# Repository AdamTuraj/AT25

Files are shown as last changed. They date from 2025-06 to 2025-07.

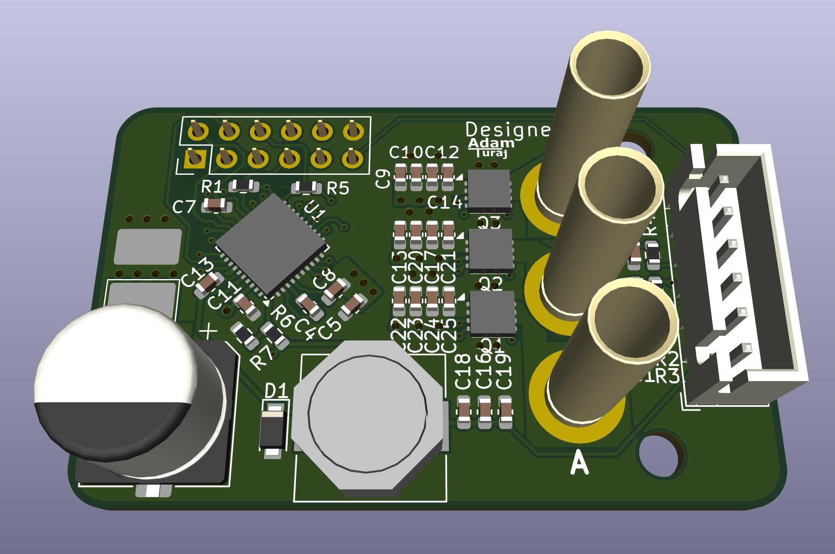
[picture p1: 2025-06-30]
Hardware/Motor_Driver/Images/3D View.png

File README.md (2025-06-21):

# AT25 - A cooler RC Car

The goal of this project is to build experience for a potential future in motorsports / Formula Student. As a fan of road car racing, I will be designing the aero and suspension car roughly around the LMGT3 regulations.

### Requirements

Below are the goals of this project. The self-imposed regulations I will be following when designing the car:

- Aerodynamic elements that work and are CFD optimized
- Double Wishbone suspension
- AWD with one sensored brushless motors
- Braking with the electric motor
- Mostly made of plastic with the exception of:
  - Gearing in the diffs
  - The electronic parts
  - The wheels
  - Any gaskets that may be required
  - Fasteners
- Remote controlled
- Fits a Lego mini figure in a driver seat

### Journal

I will be recording my day to day work in a journal found [here](https://github.com/AdamTuraj/AT25/blob/main/JOURNAL.md)

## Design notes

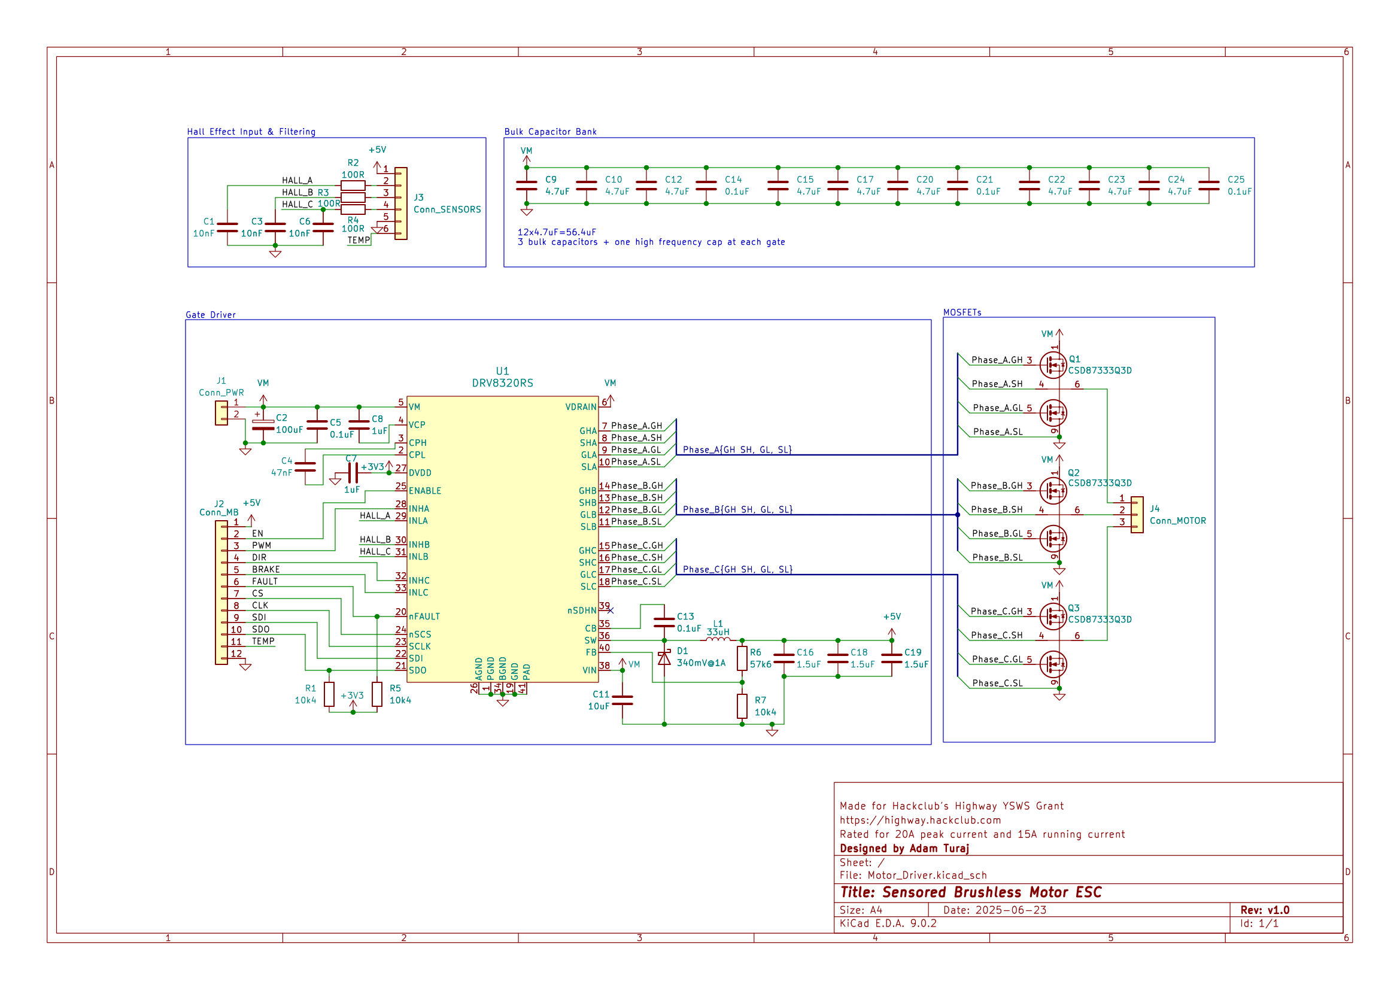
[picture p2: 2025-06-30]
Hardware/Motor_Driver/Images/Schematic.png

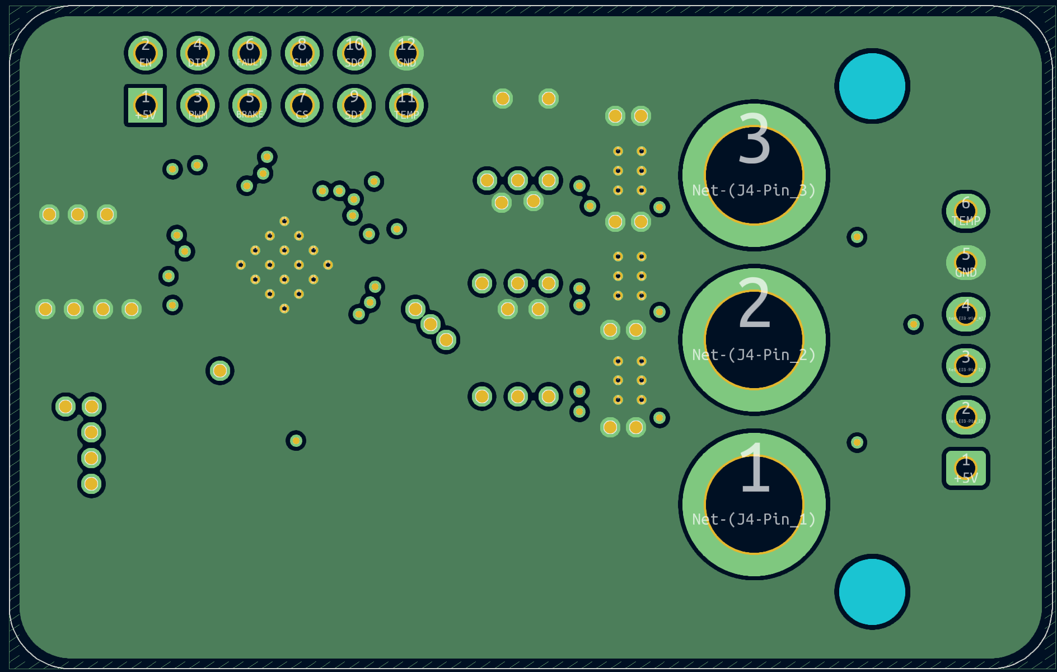
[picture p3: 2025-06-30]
Hardware/Motor_Driver/Images/2nd (GND).png

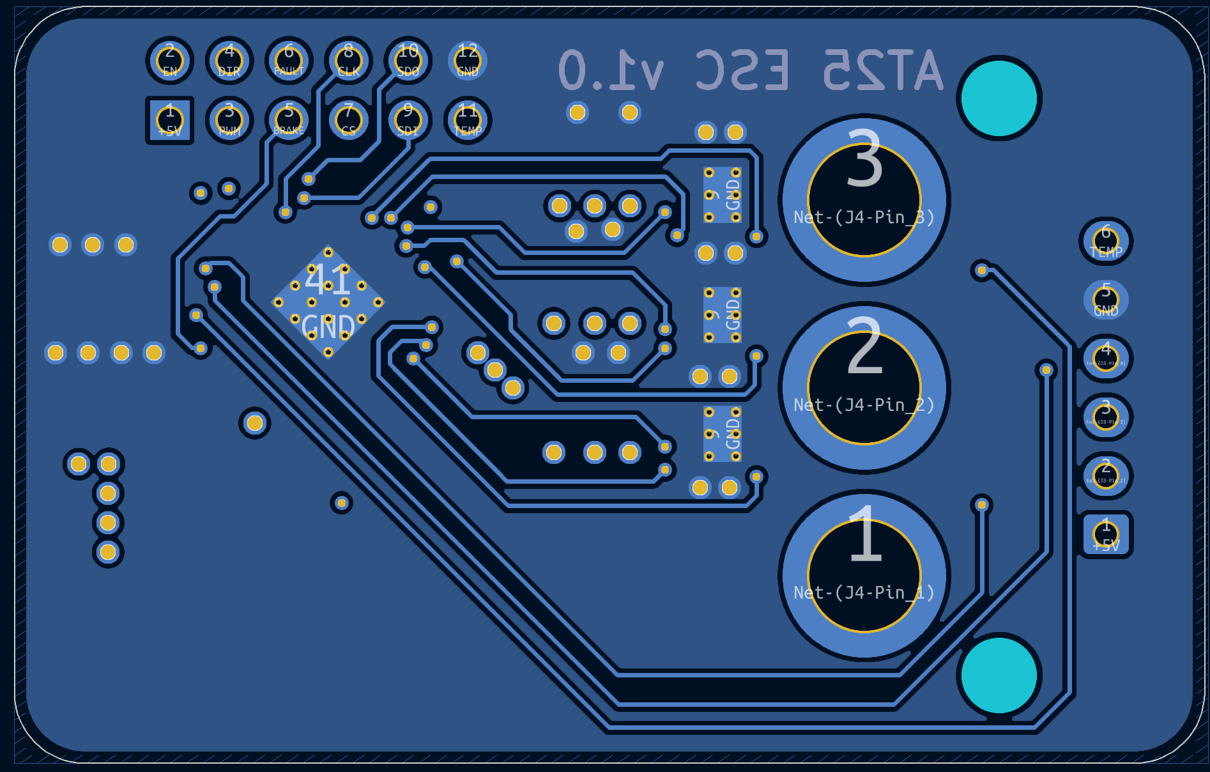
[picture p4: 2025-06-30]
Hardware/Motor_Driver/Images/Bottom (Sig).png

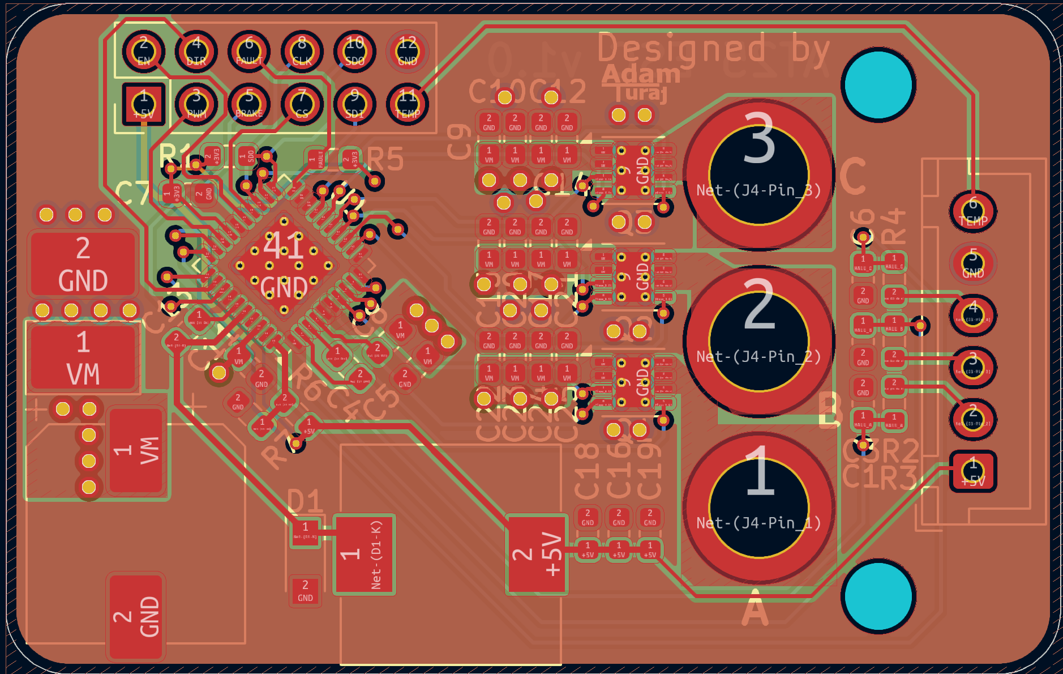
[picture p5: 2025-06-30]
Hardware/Motor_Driver/Images/All Layers.png

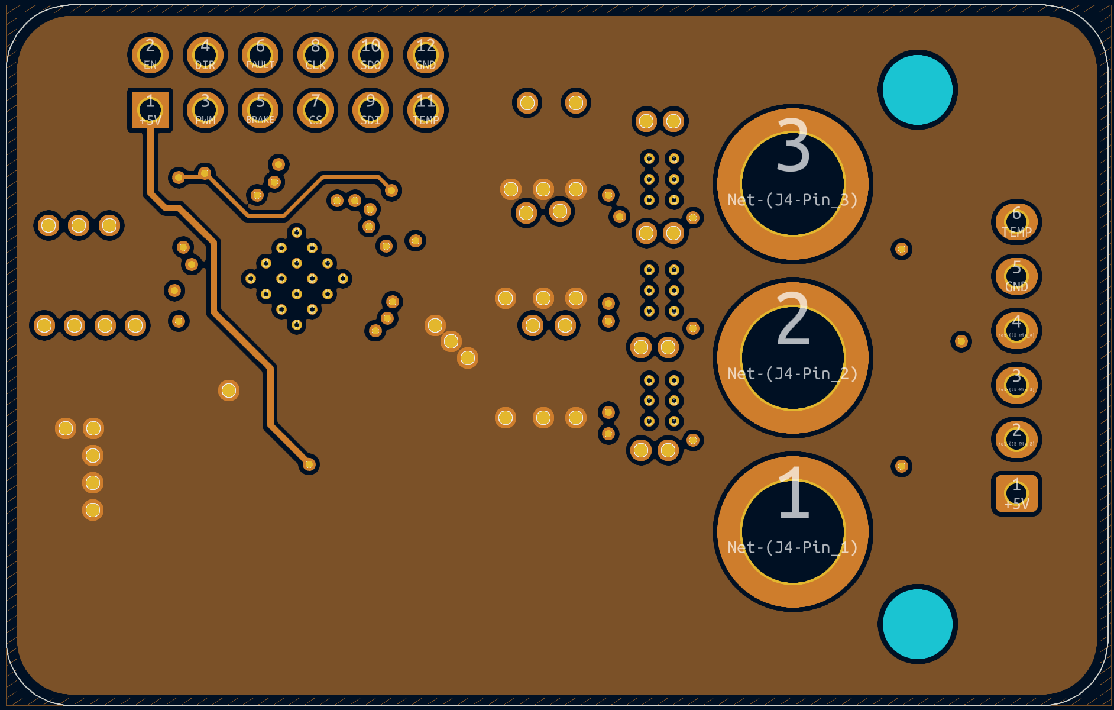
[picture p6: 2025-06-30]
Hardware/Motor_Driver/Images/3rd (PWR).png

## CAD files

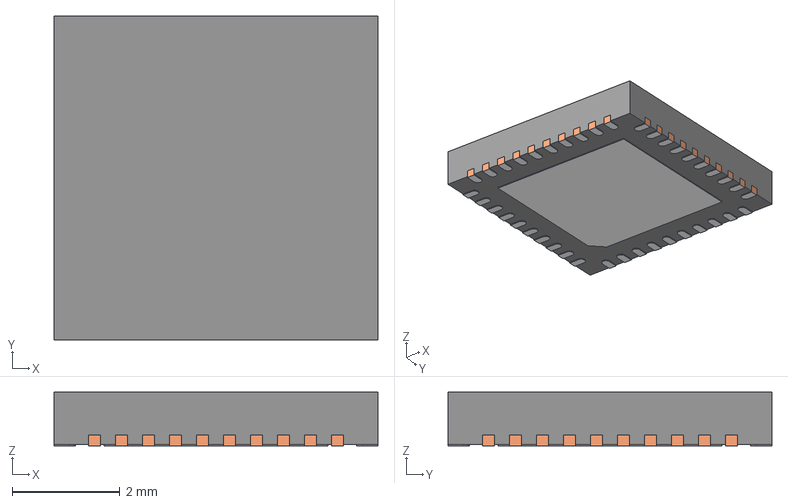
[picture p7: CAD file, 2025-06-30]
Hardware/Motor_Driver/STEP/RHA0040B.stp
6.00 x 6.00 x 1.00 mm
BODY-QFN
FRAME-RHA0040B
PIN1-ID

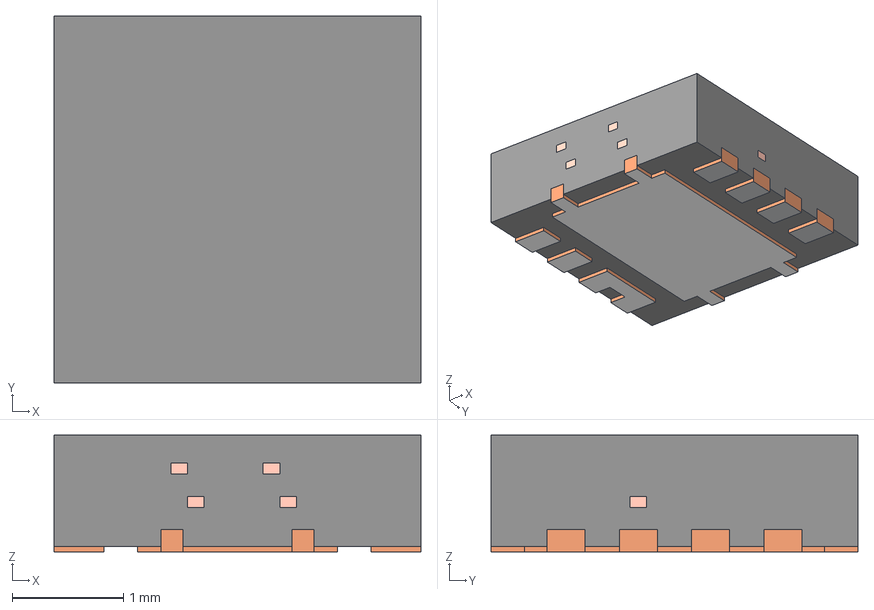
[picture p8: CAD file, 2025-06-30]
Hardware/Motor_Driver/STEP/DPB0008A.stp
3.30 x 3.30 x 1.05 mm
BODY-SON
FRAME-DPB0008A
DPB0008A_CLIP

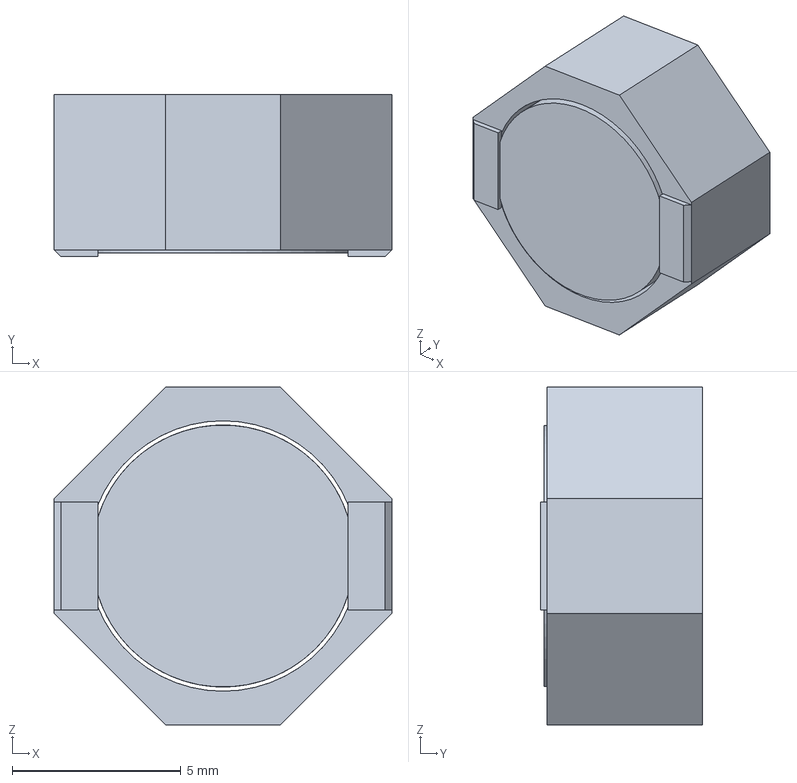
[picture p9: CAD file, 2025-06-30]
Hardware/Motor_Driver/STEP/sru1048.stp
10.0 x 4.80 x 10.0 mm

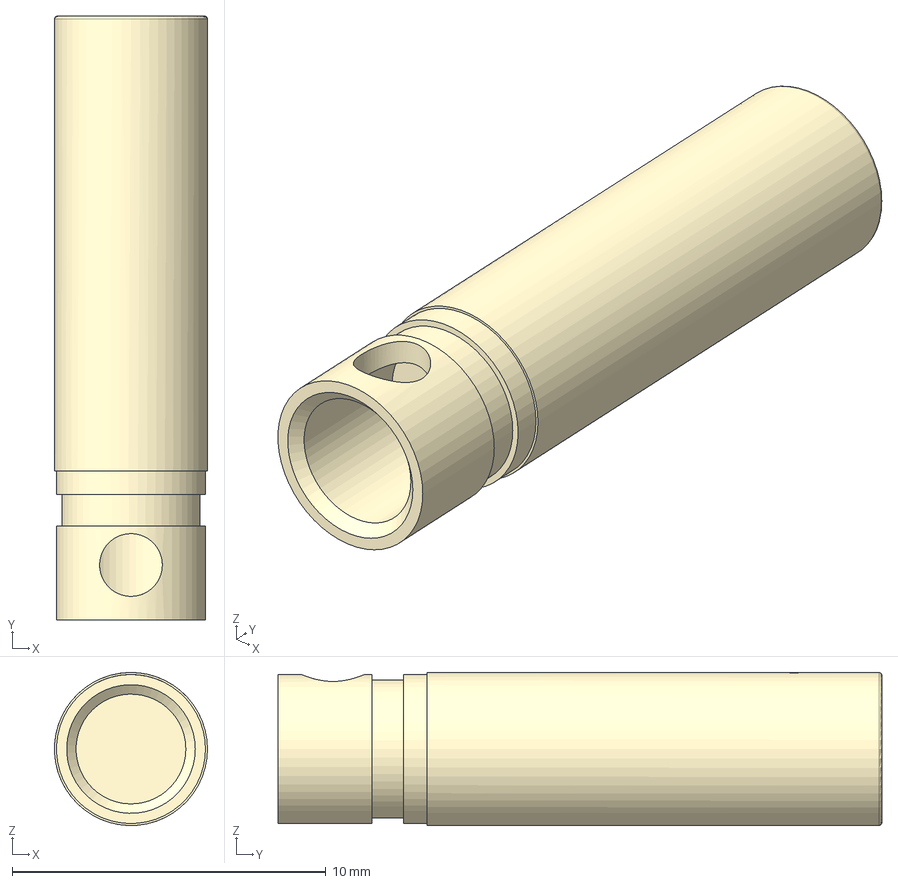
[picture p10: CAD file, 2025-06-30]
Hardware/Motor_Driver/STEP/Female_4mm_Bullet_Connector.step
4.88 x 19.2 x 4.88 mm

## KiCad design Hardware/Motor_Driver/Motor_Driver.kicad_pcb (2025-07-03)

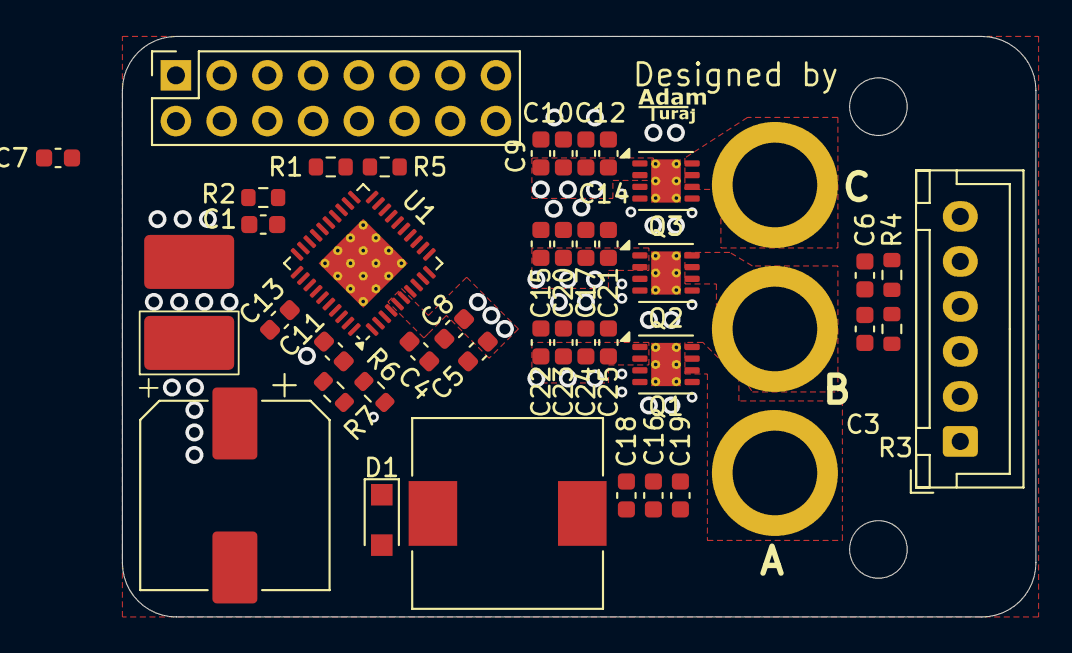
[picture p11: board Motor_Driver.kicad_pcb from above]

Board: 4 copper layers, 50.8 x 32.2 mm, 42 parts (0 on the bottom side), 38 nets, no tracks yet.

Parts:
C1, C3, C6: 10nF; C_0603_1608Metric
C2: 100uF; CP_Elec_10x10
C4: 47nF; C_0603_1608Metric
C5, C13, C14, C21, C25: 0.1uF; C_0603_1608Metric
C7, C8: 1uF; C_0603_1608Metric
C9, C10, C12, C15, C17, C20, C22, C23, C24: 4.7uF; C_0603_1608Metric
C11: 10uF; C_0603_1608Metric
C16, C18, C19: 1.5uF; C_0603_1608Metric
D1: 340mV@1A; Nexperia_CFP3_SOD-123W
J1: Conn_PWR; SolderWirePad_1x02_SMD_5x10mm
J2: Conn_MB; PinSocket_2x08_P2.54mm_Vertical
J3: Conn_SENSORS; JST_XH_B6B-XH-A_1x06_P2.50mm_Vertical
J4: Conn_MOTOR; Pin_Bullet_D4.7mm
L1: 33uH; L_10.4x10.4_H4.8
Q1, Q2, Q3: CSD87333Q3D; VSON-8-1EP_3x3mm_P0.65mm_EP1.65x2.4mm_ThermalVias
R1, R5, R7: 10k4; R_0603_1608Metric
R2, R3, R4: 100R; R_0603_1608Metric
R6: 57k6; R_0603_1608Metric
U1: DRV8320RS; VQFN-40-1EP_6x6mm_P0.5mm_EP3.5x3.5mm_ThermalVias

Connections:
+3V3: C7.1, R1.2, R5.2, U1.27 (DVDD)
+5V: C16.1, C18.1, C19.1, J2.2, J3.1, L1.2, R6.1
/BRAKE: J2.6, U1.33 (INLC)
/CLK: J2.9, U1.23 (SCLK)
/CS: J2.8, U1.24 (nSCS)
/DIR: J2.5, U1.32 (INHC)
/EN: J2.3, U1.25 (ENABLE)
/FAULT: J2.7, R5.1, U1.20 (nFAULT)
/HALL_A: C1.1, J2.13, R2.1, U1.29 (INLA)
/HALL_B: C3.1, J2.14, R3.1, U1.30 (INHB)
/HALL_C: C6.1, J2.15, R4.1, U1.31 (INLB)
/PWM: J2.4, U1.28 (INHA)
/Phase_A.GH: Q1.3 (T_{G}), U1.7 (GHA)
/Phase_A.GL: Q1.5 (B_{G}), U1.9 (GLA)
/Phase_A.SH: Q1.4 (T_{GR}), U1.8 (SHA)
/Phase_B.GH: Q2.3 (T_{G}), U1.14 (GHB)
/Phase_B.GL: Q2.5 (B_{G}), U1.12 (GLB)
/Phase_B.SH: Q2.4 (T_{GR}), U1.13 (SHB)
/Phase_C.GH: Q3.3 (T_{G}), U1.15 (GHC)
/Phase_C.GL: Q3.5 (B_{G}), U1.17 (GLC)
/Phase_C.SH: Q3.4 (T_{GR}), U1.16 (SHC)
/SDI: J2.10, U1.22 (SDI)
/SDO: J2.11, R1.1, U1.21 (SDO)
/TEMP: J2.12, J3.6
GND: C1.2, C2.2, C3.2, C5.2, C6.2, C7.2, C9.2, C10.2, C11.2, C12.2, C14.2, C15.2, C16.2, C17.2, C18.2, C19.2, C20.2, C21.2, C22.2, C23.2, C24.2, C25.2, D1.2 (A), J1.2, J2.16, J3.5, Q1.9 (P_{GND}), Q2.9 (P_{GND}), Q3.9 (P_{GND}), R7.2, U1.1 (PGND), U1.10 (SLA), U1.11 (SLB), U1.18 (SLC), U1.19 (GND), U1.26 (AGND), U1.34 (BGND), U1.41 (PAD)
unnamed: C13.2, D1.1 (K), L1.1, U1.36 (SW)
unnamed: J3.2, R2.2
unnamed: J3.3, R3.2
unnamed: J3.4, R4.2
unnamed: J4.1, Q1.6 (V_{SW}), Q1.7 (V_{SW}), Q1.8 (V_{SW})
unnamed: J4.2, Q2.6 (V_{SW}), Q2.7 (V_{SW}), Q2.8 (V_{SW})
unnamed: J4.3, Q3.6 (V_{SW}), Q3.7 (V_{SW}), Q3.8 (V_{SW})
unnamed: C13.1, U1.35 (CB)
unnamed: C4.1, U1.3 (CPH)
unnamed: C4.2, U1.2 (CPL)
unnamed: R6.2, R7.1, U1.40 (FB)
unnamed: C8.2, U1.4 (VCP)
VM: C2.1, C5.1, C8.1, C9.1, C10.1, C11.1, C12.1, C14.1, C15.1, C17.1, C20.1, C21.1, C22.1, C23.1, C24.1, C25.1, J1.1, J2.1, Q1.1 (V_{IN}), Q1.2 (V_{IN}), Q2.1 (V_{IN}), Q2.2 (V_{IN}), Q3.1 (V_{IN}), Q3.2 (V_{IN}), U1.5 (VM), U1.6 (VDRAIN), U1.38 (VIN)

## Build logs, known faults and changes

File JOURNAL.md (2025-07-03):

---
title: "AT25"
author: "Adam Turaj"
description: "A GT3 inspired RC car"
created_at: "2025-06-16"
---

# AT25 Journal

This journal will document my findings and progress throughout the project.

## Day 1 (June 19th)

**Time Spent**: 3

**Total Time on Project**: 3

---

Day 1 involved researching and selecting the necessary components. I plan to order most of the parts from GreatHobbies, a Canadian hobby store.

Initially, I selected the battery based on my preferred voltage of 7.4V due to the availability of batteries and motors, and it being at an ideal performance range. For the capacity, I opted for 5000mAh to achieve a decent runtime while remaining cost-effective.

Next, I chose the motor, which required thorough research and consideration. After evaluating the options, I decideed that using a single motor for a RWD setup would offer better cost-effectiveness and performance than 2 motor AWD. The selected motor is a 1406-2280KV, 4-pole sensored model, which can be found in the Bill of Materials (BOM).

Lastly, I selected the tires. Although I originally wanted RC slick tires, the best available option was vintage racing tires. I chose a 26mm width for the front tires and a wider 31mm for the rear.

The BOM can be found at the following link: [AT25 BOM](https://docs.google.com/spreadsheets/d/1flXe85N5WV3nN8ESYz18NZuvuu6GO_V06G4YLhqS2Ls/edit?usp=sharing)

The BOM

## Day 2 (June 20th)

**Time Spent**: 2

**Total Time on Project**: 5

---

Today, I began laying out the general design of the car. I began by learning how the aerodynamic elements work and the different elements used. Through this, I got refreshed on Bernoulli's and got a surface level understanding on how the important elements work.

Knowing this, I made a rough sketch on paper as a guideline on how I will design the car. This rough work can be found below.

Finally, I made and found the 3D models for the components I will be using. My plan is to design the aero then determine the packaging for everything else, a similar process used in F1 and other design teams.

Note: I changed the battery to a different, similar spec'd one due to a proprietary connector.

The rough sketch of the RC car

## Day 3 (June 21st)

**Time Spent**: 5

**Total Time on Project**: 10

---

In Day 3, I began work on the brushless control board. The IC pre-driver I selected was the DRV8323S due to its 1 PWM mode (no extra code required), my previous experience with it, and its availability.

I preferably would run the DRV8320S but it is out of stock so I had to compromise. This IC would be better as it doesn't include the amplifiers which are not required due to the sensored motors not needing to know the current flowing through the coils.

Afterwards, I chose the CSD87333Q3D FETs as it is TI (I love Texas Instruments), it integrates both the high and low MOSFETs, supports up to 15A (the limit I'm designing for), and the high efficiency while being cheap and available.

Drawing the schematic mainly involved following the diagrams provided by TI. It was very straightforward; however, the PCB layout will not.

The final schematic for the board is this:

Final Schematic

## Day 4 (June 22nd)

**Time Spent**: 3

**Total Time on Project**: 13

---

I did some more research while looking for footprints and came to the following conclusions:

- I will be attempting to assemble the boards myself again
- Bulk capacitor banks are required
- The DRV8320RS is preferred for my application as:
  - I do not need the current sense amplifiers (I'm using a sensored motor)
  - The buck converter is necessary for my application

Regarding conclusion #1, I will be assembling them myself due to the high costs of JLCPCB assembly, and my previous experience assembling SMD boards. I had issues assembling my last board which is the reason I was planning on using PCBA; however, I made the realization that my solder paste is expired which I believe is the source of the problems.

After making these conclusions, I adjusted my schematic to reflect them. This included updating the DRV footprint (although I haven't changed the pinout from the DRV8323RS -> DRV8320RS). The capacitance of the bulk bank was stolen from an existing open source design.

I started adding the circuitry around the buck converter but still need to fill in the values. Below is my plan on how the board will be powered:
Flow chart of power circuity

And here is the current revision of the schematic:
Current Schematic

## Day 5 (June 27th)

**Time Spent**: 7

**Total Time on Project**: 19

---

Throughout today, I tweaked the schematic, picked parts, and designed the layout.

Firstly, I made the following changes to the schematic:

- Added a RC filter to the hall effect sensors
- Adjusted the symbol to the DRV8320RS
- Finished buck converter circuitry
- Change 10uF bulk capacitor to 100uF electrolyte capacitor
- Added 0.1uF capacitors to each gate
- Cosmetic adjustments

These changes resulted in the final, completed schematic:
Completed schematic

Afterwards, I assigned footprints and picked part numbers. With all that done, I layed them out, and carefully wired them up. Due to the relatively high current and to simplify wiring, a 4 layer board was a no brainer. The stackup I used, as I have done with all my other 4 layer boards, is:

- Sig / GND
- GND
- PWR
- Sig / GND

For the first time ever, I made the entire board without a single DRC error: no clearence violations, missed connections, etc!

Below is the final design for the ESC:
3D view of PCB
PCB Layout

## Day 6 (July 2nd)

**Time Spent**: 5

**Total Time on Project**: 24

---

I began by starting the motherboard. This first involved picking the MCU which I chose to be the STM32F072. I chose it due to its small form factor (48 pins), availability, price, and it supporting all the peripherals I needed.

Afterwards, I assigned all the pins in the STM32CubeMX. I assigned:

- SWD
- USB
- DRV8320 pins (SPI + PWM, DIR, and BREAK)
- Camera SPI (for the future)
- LoRa UART
- IMU I2C
- Battery and Temperature ADC's
- The three hall effect sensors inputs

STM32CubeMX pin assignment

While assigning the pins, I fell down a rabbit hole which led to me redesigning the ESC control board to accomodate more current (25A continuous instead of 15A), adjust the bulk capacitors, and improve the routing.

I found this really good article from [Alexander Sysoev on Zubax](https://forum.zubax.com/t/how-i-learned-to-stop-worrying-and-love-esc-development/1553/5) which helped me pick the bulk capacitors, make sure the new MOSFET is sufficient for my use casee, and improve the routing.

Here is the updated ESC schematic:
ESC Schematic

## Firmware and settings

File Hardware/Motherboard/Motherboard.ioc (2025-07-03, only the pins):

Mcu.UserName=STM32F072C8Tx
PA10.GPIO_Label=MOTOR_EN
PA10.Signal=GPIO_Output
PA11.Signal=USB_DM
PA12.Signal=USB_DP
PA13.Signal=SYS_SWDIO
PA14.Signal=SYS_SWCLK
PA2.GPIO_Label=LoRa_TX
PA2.Signal=USART2_TX
PA3.GPIO_Label=LoRa_RX
PA3.Signal=USART2_RX
PA4.GPIO_Label=MOTOR_CS
PA4.Signal=GPIO_Output
PA5.GPIO_Label=MOTOR_SCK
PA5.Signal=SPI1_SCK
PA6.GPIO_Label=MOTOR_MISO
PA6.Signal=SPI1_MISO
PA7.GPIO_Label=MOTOR_MOSI
PA7.Signal=SPI1_MOSI
PA8.GPIO_Label=MOTOR_BREAK
PA8.Signal=S_TIM1_CH1
PA9.GPIO_Label=MOTOR_DIR
PA9.Signal=GPIO_Output
PB0.GPIO_Label=BATT_ADC
PB0.Signal=ADC_IN8
PB1.GPIO_Label=TEMP_ADC
PB1.Signal=ADC_IN9
PB10.GPIO_Label=CAM_SCK
PB10.Signal=SPI2_SCK
PB11.GPIO_Label=MOTOR_PWM
PB11.Signal=S_TIM2_CH4
PB14.GPIO_Label=CAM_MISO
PB14.Signal=SPI2_MISO
PB15.GPIO_Label=CAM_MOSI
PB15.Signal=SPI2_MOSI
PB2.GPIO_Label=CAM_CS
PB2.Signal=GPIO_Output
PB6.GPIO_Label=IMU_SCL
PB6.Signal=I2C1_SCL
PB7.GPIO_Label=IMU_SDA
PB7.Signal=I2C1_SDA
PC14-OSC32_IN.GPIO_Label=MOTOR_HALL1
PC14-OSC32_IN.Signal=GPIO_Input
PC15-OSC32_OUT.GPIO_Label=MOTOR_HALL2
PC15-OSC32_OUT.Signal=GPIO_Input
PF0-OSC_IN.GPIO_Label=MOTOR_HALL3
PF0-OSC_IN.Signal=GPIO_Input

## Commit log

2025-06-21 Format changes to BOM
2025-06-22 Add day 3 and schematic for the motor driver
    [Motor_Driver.kicad_pcb, Motor_Driver.kicad_sch]
2025-06-23 Day 4
    [Motor_Driver.kicad_sch]
2025-06-30 Day 5 - Finish motor driver PCB
    [DPB0008A.stp, Female_4mm_Bullet_Connector.step, Motherboard.kicad_pcb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]
2025-07-03 Day 6
    [Motherboard.kicad_sch, Motor_Driver.kicad_pcb, Motor_Driver.kicad_sch]
